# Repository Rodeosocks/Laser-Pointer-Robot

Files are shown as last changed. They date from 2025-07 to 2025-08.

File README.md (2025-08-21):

# Laser-Pointer-Robot
## To do
- [ ] finish physical design
- [ ] physically assemble it
- [ ] create trajectory generator function
- [ ] buy time of flight sensor
- [ ] increase camera fps
- [x] alter camera enclosure
- [x] figure out what to do about power cable to camera
- [x] create electronics mounting plate

## CAD
[Link to Onshape Folder](https://cad.onshape.com/documents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)  
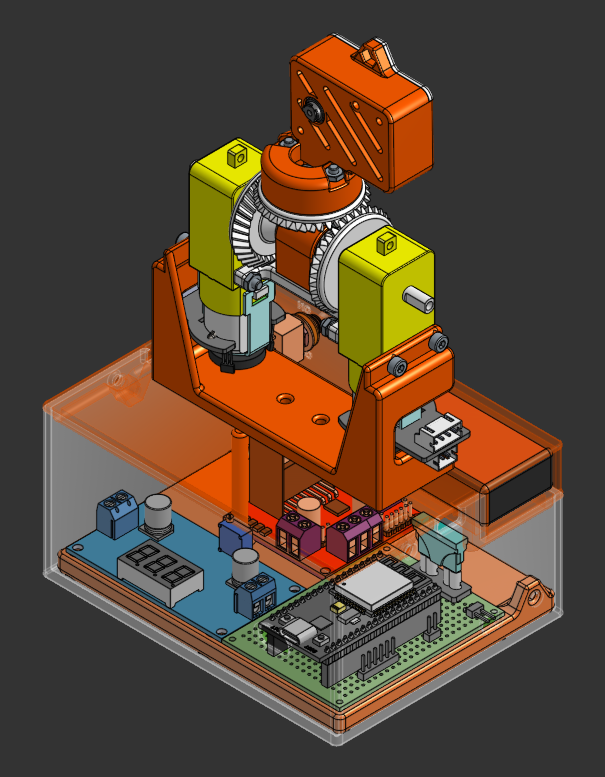
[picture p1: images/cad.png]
Differential Drive


## Electronics
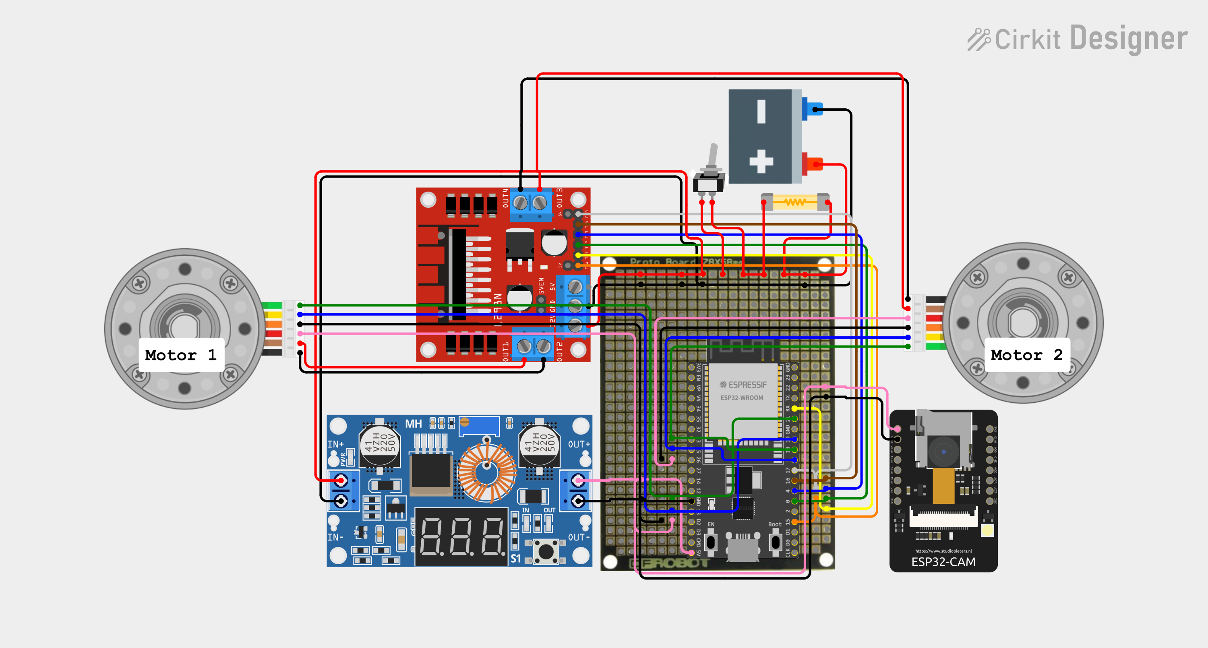
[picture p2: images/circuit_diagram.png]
Circuit Diagram

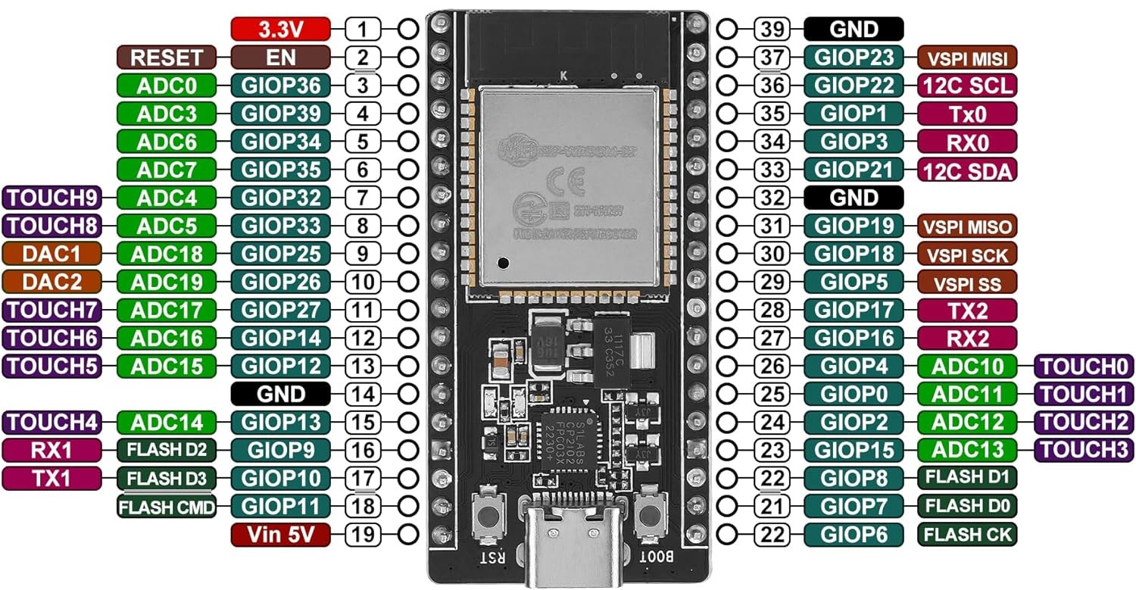
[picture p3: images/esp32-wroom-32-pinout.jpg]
ESP32 Pinout

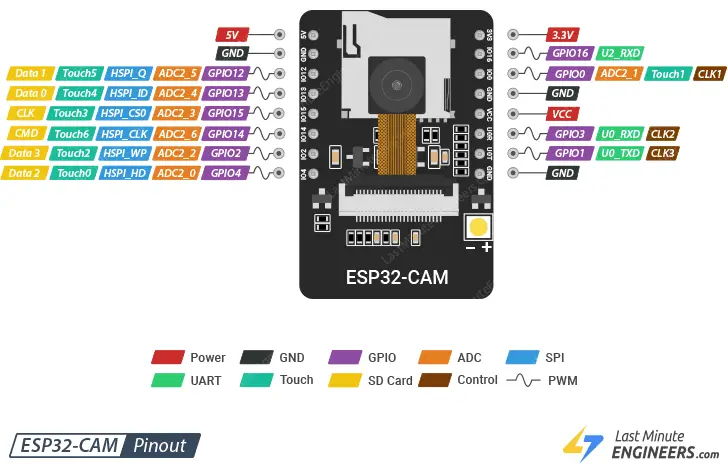
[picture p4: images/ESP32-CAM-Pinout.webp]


### Pin Table
| Pin Number | Connection |
| :---: | :---: |
| 0 | IN2 (motor driver)|
| 3 | IN1 (motor driver)|
| 4 | IN3 (motor driver)|
| 5 | EncoderB (motor 2)|
| 15 | ENA (motor driver)|
| 16 | IN4 (motor driver)|
| 17 | ENB (motor driver)|
| 18 | EncoderA (motor 2)|
| 19 | EncoderB (motor 1)|
| 21 | EncoderA (motor 1)|

## Differential Drive BOM
- [Motor Driver Board](https://www.amazon.com/dp/B0CR6BX5QL?ref=ppx_yo2ov_dt_b_fed_asin_title) - $7.56

- [Flange Bearings](https://www.amazon.com/uxcell-FR188-2RS-Flanged-Bearing-Bearings/dp/B0CH2KNZK3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) - $7.24

- [Motors](https://www.digikey.com/en/products/detail/dfrobot/FIT0450/7597205?gQT=1) - $27.22

- [ESP-32](https://www.amazon.com/ESP-WROOM-32-Development-Dual-Mode-Microcontroller-Compatible/dp/B0D53M13NS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) - $12.98

- [ESP-32-CAM](https://www.amazon.com/Aideepen-ESP32-CAM-ESP32-CAM-MB-CH-340G-NodeMCU/dp/B0CMTVFCYD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) - $12.98

- [Time of flight sensor](https://www.amazon.com/HiLetgo-VL53L0X-Distance-Measurement-Breakout/dp/B071DW8M8V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) - $6.79

- [Batteries](https://www.amazon.com/JUZUXI-Rechargeable-Connector-Compatible-Quadcopter/dp/B0DCNN87NZ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) - $17.99

- [Buck converter](https://www.amazon.com/Converter-Adjustable-Regulator-Voltmeter-Display%EF%BC%88Pack/dp/B0F1M2SR31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) - $7.99

- [Wheels](https://www.amazon.com/ThtRht-Motor-Wheels-Replacement-Smart/dp/B0CG1C7T8J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) - $8.97

## Budget
Running Total Spent: $96.16  
Predicted Total Cost: $109.72

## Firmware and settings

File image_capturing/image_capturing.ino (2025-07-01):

#include "esp_camera.h"
#include <WiFi.h>
#include "soc/soc.h"
#include "soc/rtc_cntl_reg.h"
#include "esp_http_server.h"

//-- Pinout for AI-THINKER Board --//
#define PWDN_GPIO_NUM     32
#define RESET_GPIO_NUM    -1
#define XCLK_GPIO_NUM      0
#define SIOD_GPIO_NUM     26
#define SIOC_GPIO_NUM     27
#define Y9_GPIO_NUM       35
#define Y8_GPIO_NUM       34
#define Y7_GPIO_NUM       39
#define Y6_GPIO_NUM       36
#define Y5_GPIO_NUM       21
#define Y4_GPIO_NUM       19
#define Y3_GPIO_NUM       18
#define Y2_GPIO_NUM        5
#define VSYNC_GPIO_NUM    25
#define HREF_GPIO_NUM     23
#define PCLK_GPIO_NUM     22
#define FLASH_GPIO_NUM    4

//-- Your Wi-Fi Credentials --//
const char* ssid = "Sawyer's Wifi";
const char* password = "No Spaces No Caps";

//-- Function Prototypes --//
esp_err_t capture_handler(httpd_req_t *req);

//-- Starts the web server --//
void startCameraServer() {
  httpd_handle_t server = NULL;
  httpd_config_t config = HTTPD_DEFAULT_CONFIG();

  httpd_uri_t capture_uri = {
      .uri       = "/capture",
      .method    = HTTP_GET,
      .handler   = capture_handler,
      .user_ctx  = NULL
  };
  
  if (httpd_start(&server, &config) == ESP_OK) {
    httpd_register_uri_handler(server, &capture_uri);
  }
}

//-- Main Setup --//
void setup() {
  // Disable brownout detector
  WRITE_PERI_REG(RTC_CNTL_BROWN_OUT_REG, 0); 

  Serial.begin(115200);
  Serial.setDebugOutput(false);

  // Camera configuration
  camera_config_t config;
  config.ledc_channel = LEDC_CHANNEL_0;
  config.ledc_timer = LEDC_TIMER_0;
  config.pin_d0 = Y2_GPIO_NUM;
  config.pin_d1 = Y3_GPIO_NUM;
  config.pin_d2 = Y4_GPIO_NUM;
  config.pin_d3 = Y5_GPIO_NUM;
  config.pin_d4 = Y6_GPIO_NUM;
  config.pin_d5 = Y7_GPIO_NUM;
  config.pin_d6 = Y8_GPIO_NUM;
  config.pin_d7 = Y9_GPIO_NUM;
  config.pin_xclk = XCLK_GPIO_NUM;
  config.pin_pclk = PCLK_GPIO_NUM;
  config.pin_vsync = VSYNC_GPIO_NUM;
  config.pin_href = HREF_GPIO_NUM;
  config.pin_sscb_sda = SIOD_GPIO_NUM;
  config.pin_sscb_scl = SIOC_GPIO_NUM;
  config.pin_pwdn = PWDN_GPIO_NUM;
  config.pin_reset = RESET_GPIO_NUM;
  config.xclk_freq_hz = 20000000;
  config.pixel_format = PIXFORMAT_JPEG;
  
  // Best quality for higher resolutions
  config.frame_size = FRAMESIZE_QVGA; // (320x240)
  config.jpeg_quality = 25; // 0-63 lower number means higher quality
  config.fb_count = 2;

  // Initialize camera
  esp_err_t err = esp_camera_init(&config);
  if (err != ESP_OK) {
    Serial.printf("Camera init failed with error 0x%x", err);
    return;
  }

  // Connect to Wi-Fi
  WiFi.begin(ssid, password);
  while (WiFi.status() != WL_CONNECTED) {
    delay(500);
    Serial.print(".");
  }
  Serial.println("");
  Serial.println("WiFi connected");
  Serial.print("Camera Ready! Use 'http://");
  Serial.print(WiFi.localIP());
  Serial.println("/capture' to get a frame.");

  // Turn on flash
  pinMode(FLASH_GPIO_NUM, OUTPUT);
  digitalWrite(FLASH_GPIO_NUM, HIGH);

  // Start the server
  startCameraServer();
}

//-- Main Loop --//
void loop() {
  // Keep the main loop clean
  delay(10000);
}

//-- HTTP Handler for taking a picture --//
esp_err_t capture_handler(httpd_req_t *req){
  camera_fb_t * fb = NULL;
  esp_err_t res = ESP_OK;
  
  // Take a picture
  fb = esp_camera_fb_get();
  if (!fb) {
    Serial.println("Camera capture failed");
    httpd_resp_send_500(req);
    return ESP_FAIL;
  }

  // Set HTTP response headers
  httpd_resp_set_type(req, "image/jpeg");
  httpd_resp_set_hdr(req, "Content-Disposition", "inline; filename=capture.jpg");
  httpd_resp_set_hdr(req, "Access-Control-Allow-Origin", "*");

  // Send the picture data
  res = httpd_resp_send(req, (const char *)fb->buf, fb->len);
  
  // Return the frame buffer to be reused
  esp_camera_fb_return(fb);
  
  return res;
}

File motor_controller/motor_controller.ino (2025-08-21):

// Import classes
#include "Motor.h"
#include "EndEffector.h"

// Declare pin numbers
// Motor 1
int enA = 15;
int in1 = 3;
int in2 = 0;
int enc1A = 21;
int enc1B = 19;
// Motor 2
int enB = 17;
int in3 = 4;
int in4 = 16;
int enc2A = 18;
int enc2B = 5;

// Initialize global varaibles
bool completed_move = false;
float control_time_step = 1000.0; // microseconds
unsigned long prev_time;
unsigned long time_diff;
bool already_printed = false;

// Instatiate objects
// Create encoder objects
ESP32Encoder encoder1;
ESP32Encoder encoder2;
// Create motor objects
Motor motor1(in1, in2, enA, enc1A, enc1B, encoder1);
Motor motor2(in3, in4, enB, enc2A, enc2B, encoder2);
// Create end effector object
EndEffector camera(motor1, motor2);

void setup() {
  Serial.begin(115200);
  motor1.init();
  motor2.init();
  prev_time = micros();
}

void loop() {
  time_diff = micros() - prev_time;

  
  if ((completed_move == false) && (time_diff >= control_time_step)) {
    completed_move = camera.go_to_pose(0.0, -90.0, 0.5, control_time_step);
    prev_time = micros();
  } else if ((completed_move == true) && (already_printed == false)) {
    Serial.println("Move Complete");
    already_printed = true;
  }
}

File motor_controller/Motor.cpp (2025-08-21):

#include "Motor.h"
#include <math.h>

Motor::Motor(int IN1_PIN, int IN2_PIN, int EN_PIN) {
  this->IN1_PIN = IN1_PIN;
  this->IN2_PIN = IN2_PIN;
  this->EN_PIN = EN_PIN;
  int ENC_A_PIN = -1;
}

Motor::Motor(int IN1_PIN, int IN2_PIN, int EN_PIN, int ENC_A_PIN, int ENC_B_PIN, ESP32Encoder encoder) {
  this->IN1_PIN = IN1_PIN;
  this->IN2_PIN = IN2_PIN;
  this->EN_PIN = EN_PIN;
  this->ENC_A_PIN = ENC_A_PIN;
  this->ENC_B_PIN = ENC_B_PIN;
  this->encoder = encoder;
  int count = 0;
}

void Motor::init() {
  pinMode(IN1_PIN, OUTPUT);
  pinMode(IN2_PIN, OUTPUT);
  pinMode(EN_PIN, OUTPUT);
  stop();
  if (ENC_A_PIN != -1) {
    encoder.attachHalfQuad(ENC_A_PIN, ENC_B_PIN);
    encoder.setCount(0);
  }
}

void Motor::forward(float speed) {
  speed = 1000 * constrain(speed, 0.0, 1.0);
  int speed_mapped = map(speed, 0, 1000, 76, 255);
  analogWrite(EN_PIN, speed_mapped);
  digitalWrite(IN2_PIN, LOW);
  digitalWrite(IN1_PIN, HIGH);
}

void Motor::backward(float speed) {
  speed = 1000 * constrain(speed, 0.0, 1.0);
  int speed_mapped = map(speed, 0, 1000, 76, 255);
  analogWrite(EN_PIN, speed_mapped);
  digitalWrite(IN2_PIN, HIGH);
  digitalWrite(IN1_PIN, LOW);
}

void Motor::stop() {
  analogWrite(EN_PIN, 0);
  digitalWrite(IN1_PIN, LOW);
  digitalWrite(IN2_PIN, LOW);
}

void Motor::print_count() {
  Serial.println(encoder.getCount() / 2);
}

bool Motor::go_to_angle(float target_angle) {
  if (started_move == false) {
    // Convert angle (in deg) to encoder count
    int target_encoder_diff = int(round(target_angle * (1 / 360.0) * 960.0));
    started_move = true;
    target_encoder_count = target_encoder_diff + (encoder.getCount() / 2);
    prev_error = target_encoder_count - (encoder.getCount() / 2);
    prev_time = micros();
  }

  // Constant speed control until tolerance is reach (tol ~= +/- 1 deg)
  int error = target_encoder_count - (encoder.getCount() / 2);
  unsigned long time = micros();
  float d_error = -1.0 * (float(error) - float(prev_error)) / (time - prev_time);
  float speed = (error * (1 / 345.0)) + (d_error * 10);

  if (abs(error) > 3) {
    completed_move = false;
    if (error > 0) {
      forward(abs(speed));
    } else {
      backward(abs(speed));
    }
  } else {
    stop();
    started_move = false;
    completed_move = true;
  }

  prev_error = error;
  prev_time = time;
  return completed_move;
}

float Motor::get_angle() {
  int enc_count = encoder.getCount() / 2;
  float large_angle = (360.0 / 960.0) * float(enc_count);
  // normalize angle from -180 -> 180
  float angle = fmod(large_angle, 360.0);
  if (angle < -180.0) {
    angle += 360.0;
  }
  return angle;
}

int Motor::get_count() {
  return (encoder.getCount() / 2);
}

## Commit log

2025-07-01 Add differential drive circuit diagram
2025-07-03 Add initial motor control sketch
2025-07-04 Add motor class to handle motor driver and encoder
2025-07-04 Create fritzing diagram
    [circuit_diagram.fzz]
2025-07-05 Add basic motor control by angle
2025-07-08 Add electronics housing and circuit design to CAD
2025-07-08 Redo circuit diagram with protoboard and pin header positions
2025-08-18 Started tuning motor gains, major CAD revision (see OnShape V5)
2025-08-20 Tune gains, add get_angle function to Motor class, add EndEffector class with get_roll and get_pitch methods
2025-08-20 Add pin table, update to do list
